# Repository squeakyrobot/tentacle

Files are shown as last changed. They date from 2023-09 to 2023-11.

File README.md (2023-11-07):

# tentacle
Modular robotic tentacle

TODO: On the project webpage add a simple calculator to help with the tentacle setup that allows the user to
easily configure their tentacle. Also add the maths in this document

## BOM

 * Internal Bearings - [F683ZZ](https://www.amazon.com/gp/product/B07Z3DRZX9)
 * Pulley Bearings - [6700-2RS](https://www.amazon.com/gp/product/B082PR3DFZ)

## Motor Options

## 28BYJ-48
I modified these motors to be bipolar, See [this article](https://ardufocus.com/howto/28byj-48-bipolar-hw-mod/)

## TODO:

- Add NEMA-11 support
- Add NEMA-14 support
- Test different configurations
    - Spine size
        - 4mm OD, 3mm ID
        - 4mm OD, 2mm ID
        - 6mm OD, 3mm ID
    - Cable materials

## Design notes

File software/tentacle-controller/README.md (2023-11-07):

# tentacle-controller

## TODO: 
 
 - Use enable pin on/off for when the movement is stopped: GPIO19, CTRL pin 3
 - Add support for controlling two motors with one timer
 - Add readme content
 - ACCESSORY: Use TMF8820 or equivalent for homing?

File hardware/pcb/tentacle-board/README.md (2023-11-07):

# Tentacle Controller PCB

TODO: Add more details about the board

## Pinout

Both motors share microstep configuration pins and the enable pin.

### Microstep Configuration

| **DRV8825 Pin** 	| **RP2040 Pin** 	|
|---	|---	|
| MODE 0 	| GPIO3 	|
| MODE 1 	| GPIO2 	|
| MODE 2 	| GPIO1 	|

### Motor A

| **DRV8825 Pin** 	| **RP2040 Pin** 	|
|---	|---	|
| DIR 	| GPIO6 	|
| STEP 	| GPIO4 	|
| ENABLE 	| GPIO5 	|
| SLEEP 	| GPIO8 	|
| RESET 	| GPIO9 	|
| HOME 	| GPIO0 	|
| FAULT 	| GPIO7 	|

### Motor B

| **DRV8825 Pin** 	| **RP2040 Pin** 	|
|---	|---	|
| DIR 	| GPIO12 	|
| STEP 	| GPIO11 	|
| ENABLE 	| GPIO5 	|
| SLEEP 	| GPIO14 	|
| RESET 	| GPIO15 	|
| HOME 	| GPIO10 	|
| FAULT 	| GPIO13 	|

### Debug Connector

| **Connector Pin** | **RP2040 Pin** |
|---	|---|
| 1 	| SWCLK |
| 2 	 | GND 	 |
| 3 	 | SWD 	 |

### UART Connector

| **Connector Pin** | **RP2040 Pin** | **Pin Functions** |
|---	|--- |--- |
| 1 	| GPIO17 | UART0 RX |
| 2 	 | GND 	 | |
| 3 	 | GPIO16 | UART0 TX |

### CTRL Connector

| **Connector Pin** | **RP2040 Pin** | **Pin Functions** |
|---	|--- |--- |
| 1 	| GND | |
| 2 	 | RUN 	 | Reset when driven low |
| 3 	 | GPIO19 | |
| 4 	 | GPIO20 | UART1 TX, I2C0 SDA |
| 5 	 | GPIO21 | UART1 RX, I2C0 SCL |

### AUX1 Connector

| **Connector Pin** | **RP2040 Pin** | **Pin Functions** |
|---	|--- |--- |
| 1 	| GND | |
| 2 	 | GPIO22 	 | |
| 3 	 | GPIO23 | |
| 4 	 | GPIO24 | |
| 5 	 | GPIO25 | |

### AUX2 Connector

| **Connector Pin** | **RP2040 Pin** | **Pin Functions** |
|---	|--- |--- |
| 1 	| GND | |
| 2 	 | GPIO26 	 | ADC0 |
| 3 	 | GPIO27 | ADC1 |
| 4 	 | GPIO28 | ADC2 |
| 5 	 | GPIO29 | ADC3 |

### Motor Connectors

All motor connectors map to the same pins of their corresponding DRV8825 modules 

| **Connector Pin** | **DRV8825 Pin** |
|---	|---	|
| 1 	| B2 	 |
| 2 	 | B1 	 |
| 3 	 | A1 	 |
| 4 	 | A2 	 |

## Revision History

### v1.0

 * Initial Release

### v1.1

 * **NOT COMPLETE**
 * Fix issue with missing silkscreen items

## TODO:

 * Investigate alternative motor connectors
    - Change to JST-PH 2mm
 * Investigate alternative power connector
 * Switch interface connectors to right angle
 * Switch to a shared SLEEP and individual ENABLE
 * Add software configurable VREF, perhaps have the pot be the max
 * Make CTRL & AUX connectors 90 degrees

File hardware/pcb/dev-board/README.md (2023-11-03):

# Development Board

TODO: Add more details about the board

## Pinout

### Microstep Configuration

Both motors share microstep configuration pins

| **DRV8825 Pin** 	| **Pico Pin** 	|
|---	|---	|
| MODE 0 	| GPIO2 	|
| MODE 1 	| GPIO3 	|
| MODE 2 	| GPIO4 	|

### Motor 1

| **DRV8825 Pin** 	| **Pico Pin** 	 |
|---	|--- |
| DIR 	| GPIO7 	|
| STEP 	| GPIO6 	|
| ENABLE 	| GND 	 |
| SLEEP 	| GPIO8 	|
| RESET 	| GND 	 |
| FAULT 	| GND 	 |

### Motor 2

| **DRV8825 Pin** 	| **Pico Pin** 	 |
|---	|--- |
| DIR 	| GPIO10 	|
| STEP 	| GPIO9 	|
| ENABLE 	| GND 	 |
| SLEEP 	| GPIO8 	|
| RESET 	| GND 	 |
| FAULT 	| GND 	 |

### Motor 3

| **DRV8825 Pin** 	| **Pico Pin** 	 |
|---	|--- |
| DIR 	| GPIO13 	|
| STEP 	| GPIO12 	|
| ENABLE 	| GND 	 |
| SLEEP 	| GPIO11 	|
| RESET 	| GND 	 |
| FAULT 	| GND 	 |

### Motor 4

| **DRV8825 Pin** 	| **Pico Pin** 	 |
|---	|--- |
| DIR 	| GPIO16 	|
| STEP 	| GPIO15 	|
| ENABLE 	| GND 	 |
| SLEEP 	| GPIO14 	|
| RESET 	| GND 	 |
| FAULT 	| GND 	 |

### Motor Connectors

All motor connectors map to the same pins of their corresponding DRV8825 modules 

| **Connector Pin** | **DRV8825 Pin** |
|---	|---	|
| 1 	| B2 	 |
| 2 	 | B1 	 |
| 3 	 | A1 	 |
| 4 	 | A2 	 |

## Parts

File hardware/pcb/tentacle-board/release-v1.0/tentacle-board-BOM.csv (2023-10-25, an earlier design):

Id | Designator | Footprint | Quantity | Designation | LCSC Part Number
1 | C37,C30,C10 | C_0805_2012Metric | 3 | 10uF | C15850
2 | C12,C11 | C_0402_1005Metric | 2 | 1uF | C107372
3 | C25,C15,C8,C27,C28,C29,C31,C32,C14,C34 | C_0402_1005Metric | 10 | 100nF | C60474
4 | U3 | SOT-223-3_TabPin2 | 1 | NCP1117-3.3_SOT223 | C2902118
5 | C26,C33 | C_0402_1005Metric | 2 | 30pF | C107004
6 | U4 | RP2040-QFN-56 | 1 | RP2040 | C2040
7 | R11 | C_0402_1005Metric | 1 | 1k | C11702
8 | Y1 | ABM810000MHZ12D2W | 1 | ABM8-12.000MHZ-20-B1U-T | C133334
9 | VR1 | TC33X2503E | 1 | TC33X-2-103E | C719176
10 | J7,J2,J5 | JST_SH_BM05B-SRSS-TB_1x05-1MP_P1.00mm_Vertical | 1 | JST_SH_BM05B | C160391
11 | L7,L6,L2,L8,L5,L1,L3,L4 | L_0805_2012Metric | 8 | L_Ferrite | C369519
12 | R6,R3,R4,R10 | R_0402_1005Metric_Pad0.72x0.64mm_HandSolder | 4 | 0.1ohms | C3013344
13 | R5,R1 | R_0402_1005Metric_Pad0.72x0.64mm_HandSolder | 2 | 1M | C138033
14 | C20,C2,C22,C23,C5,C6,C36,C7 | C_0805_2012Metric | 8 | 1nF | C51210
15 | C35,C17 | C_0603_1608Metric | 2 | 0.47uF | C577418
17 | J4,J1 | JST_XH_B4B-XH-A_1x04_P2.50mm_Vertical | 2 | Motor | C37815
18 | J6,J3 | JST_SH_BM03B-SRSS-TB_1x03-1MP_P1.00mm_Vertical | 1 | BM03B-SRSS | C160389
19 | C4,C19 | C_0603_1608Metric_Pad1.08x0.95mm_HandSolder | 2 | 10nF | C100042
20 | C3,C16,C1,C18,C21,C13 | C_0603_1608Metric_Pad1.08x0.95mm_HandSolder | 6 | 0.1uf | C3011705
21 | R12,R7,R2 | R_0402 | 2 | 10k | C60490
23 | C9,C24 | CAPAE660X800N | 2 | 100uF | C250945
24 | U1,U2 | IC_TPS61196PWPRQ1 | 2 | DRV8825PWP | C81582
25 | IC1 | SON127P600X500X80-9N-D | 1 | W25Q32JVZPIQ | C571260
26 | R9,R8,R13 | R_0402_1005Metric_Pad0.72x0.64mm_HandSolder | 3 | 1.5k | C114759
29 | J8 | JST_XH_B2B-XH-A_1x02_P2.50mm_Vertical | 1 | Power | C442299

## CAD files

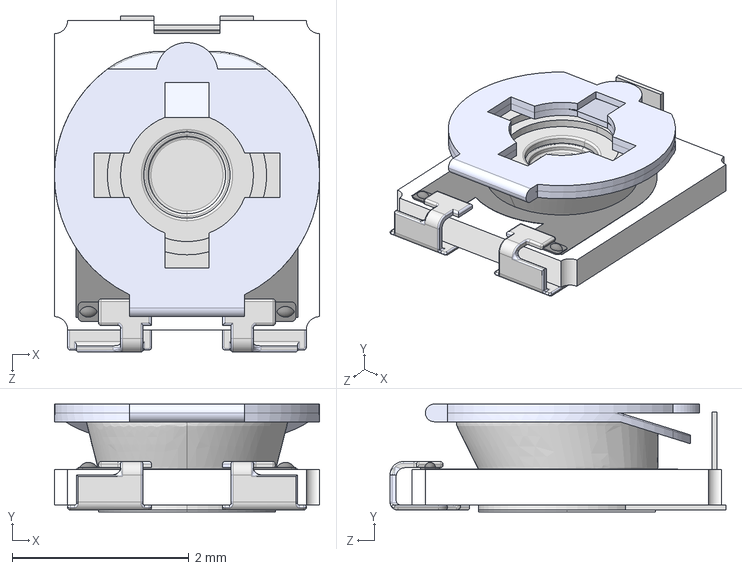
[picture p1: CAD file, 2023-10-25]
hardware/pcb/tentacle-board/3dshapes/TC33X-2-103E.stp
3.00 x 1.22 x 3.80 mm

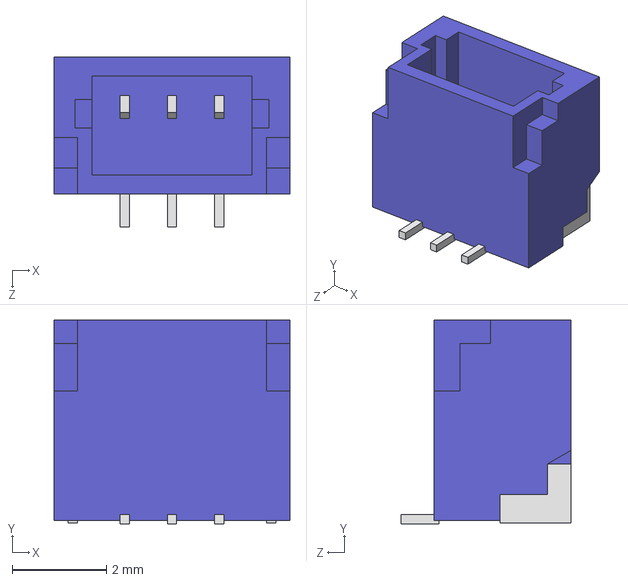
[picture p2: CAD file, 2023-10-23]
hardware/pcb/tentacle-board/3dshapes/BM03B-SRSS-TB.STEP
5.00 x 4.32 x 3.60 mm

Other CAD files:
hardware/cad/printing/assembly-tools/solder-jig.stl
hardware/cad/printing/base-lid_28BYJ-48_insert-venty.stl
hardware/cad/printing/test-stand/tent-stand-leg.stl
hardware/cad/printing/X1C/tentacle-all.3mf
hardware/cad/termination-vertebrae.step
hardware/pcb/dev-board/3dshapes/CON-SOCJ-2155.step
hardware/pcb/tentacle-board/tentacle-board.step
hardware/printing/base-lid_28BYJ-48-6-bearings.stl
hardware/cad/printing/assembly-tools/pulley-cap.stl
hardware/cad/printing/Pulley-28BYJ-48_A.stl
hardware/cad/printing/test-stand/tent-stand-top-table.stl
hardware/cad/printing/X1C/base.3mf
hardware/cad/printing/assembly-tools/termination-hold-down-jig.stl
hardware/cad/printing/base-lid-board-mount.stl
hardware/cad/printing/test-stand/tent-stand-base.stl
hardware/cad/printing/X1C/Pulley-28BYJ-48_PC.3mf
hardware/cad/printing/6mm-quick-connect-clip.stl
hardware/cad/printing/Pulley-28BYJ-48_B.stl
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

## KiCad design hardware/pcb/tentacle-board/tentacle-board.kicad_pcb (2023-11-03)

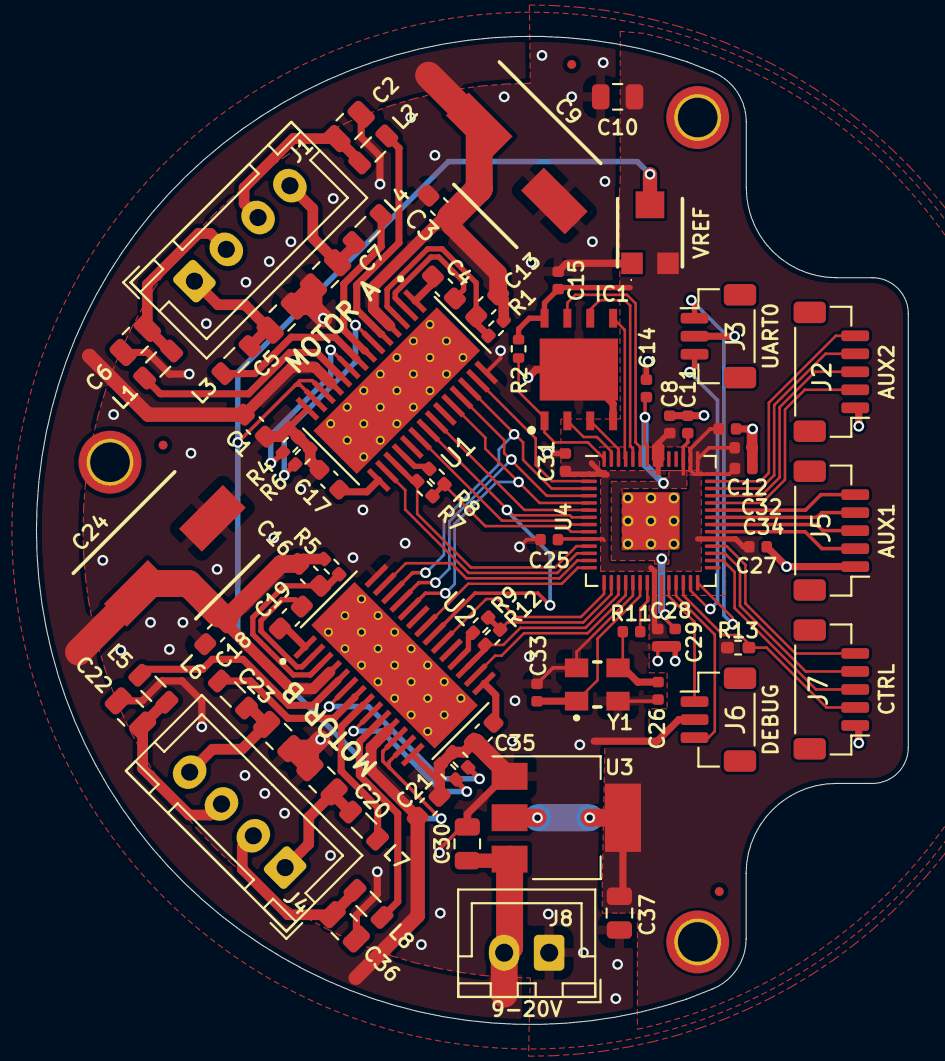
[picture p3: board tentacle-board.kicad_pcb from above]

Board: 2 copper layers, 48.4 x 54.9 mm, 79 parts (0 on the bottom side), 76 nets.

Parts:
C1, C3, C13, C16, C18, C21: 0.1uf; C_0603_1608Metric_Pad1.08x0.95mm_HandSolder
C2, C5, C6, C7, C20, C22, C23, C36: 1nF; C_0805_2012Metric
C4, C19: 10nF; C_0603_1608Metric_Pad1.08x0.95mm_HandSolder
C8, C14, C15, C25, C27, C28, C29, C31, C32, C34: 100nF; C_0402_1005Metric
C9, C24: 100uF; CAPAE660X800N
C10, C30, C37: 10uF; C_0805_2012Metric
C11, C12: 1uF; C_0402_1005Metric
C17, C35: 0.47uF; C_0603_1608Metric
C26, C33: 30pF; C_0402_1005Metric
FID1, FID2, FID3: Fiducial; Fiducial_0.5mm_Mask1mm
H1, H2, H3: MountingHole; MountingHole_2.2mm_M2_ISO7380_Pad_TopBottom
IC1: W25Q32JVZPIQ; SON127P600X500X80-9N-D
J1, J4: Motor; JST_XH_B4B-XH-A_1x04_P2.50mm_Vertical
J2: AUX2; JST_SH_BM05B-SRSS-TB_1x05-1MP_P1.00mm_Vertical
J3: UART0; JST_SH_BM03B-SRSS-TB_1x03-1MP_P1.00mm_Vertical
J5: AUX1; JST_SH_BM05B-SRSS-TB_1x05-1MP_P1.00mm_Vertical
J6: DEBUG; JST_SH_BM03B-SRSS-TB_1x03-1MP_P1.00mm_Vertical
J7: CTRL; JST_SH_BM05B-SRSS-TB_1x05-1MP_P1.00mm_Vertical
J8: Conn_01x02; JST_XH_B2B-XH-A_1x02_P2.50mm_Vertical
L1, L2, L3, L4, L5, L6, L7, L8: L_Ferrite; L_0805_2012Metric
R1, R5: 1M; R_0402_1005Metric_Pad0.72x0.64mm_HandSolder
R2: 10k; R_0402_1005Metric
R3, R4, R6, R10: 0.1; R_0402_1005Metric_Pad0.72x0.64mm_HandSolder
R7, R12: 10k; R_0402_1005Metric_Pad0.72x0.64mm_HandSolder
R8, R9, R13: 1.5k; R_0402_1005Metric_Pad0.72x0.64mm_HandSolder
R11: 1k; C_0402_1005Metric
U1, U2: DRV8825PWP; IC_TPS61196PWPRQ1
U3: NCP1117-3.3_SOT223; SOT-223-3_TabPin2
U4: RP2040; RP2040-QFN-56
VR1: TC33X-2-103E; TC33X2503E
Y1: ABM8-12.000MHZ-20-B1U-T; ABM810000MHZ12D2W

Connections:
+1V1: C11.1, C14.1, C29.1, U4.23 (DVDD), U4.45 (VREG_VOUT), U4.50 (DVDD)
+3V3: C8.1, C10.1, C12.1, C15.1, C25.1, C27.1, C28.1, C31.1, C32.1, C34.1, C37.1, IC1.8 (VCC), R2.1, R13.2, U3.2 (VO), U4.1 (IOVDD), U4.10 (IOVDD), U4.22 (IOVDD), U4.33 (IOVDD), U4.42 (IOVDD), U4.43 (ADC_AVDD), U4.44 (VREG_IN), U4.48 (USB_VDD), U4.49 (IOVDD), VR1.3 (CW)
/GPIO0: U1.27 (NHOME), U4.2 (GPIO0)
/GPIO1: U1.26 (MODE2), U2.26 (MODE2), U4.3 (GPIO1)
/GPIO2: U1.25 (MODE1), U2.25 (MODE1), U4.4 (GPIO2)
/GPIO3: U1.24 (MODE0), U2.24 (MODE0), U4.5 (GPIO3)
/GPIO4: U1.22 (STEP), U4.6 (GPIO4)
/GPIO5: U1.21 (NENBL), U2.21 (NENBL), U4.7 (GPIO5)
/GPIO6: U1.20 (DIR), U4.8 (GPIO6)
/GPIO7: R7.1, R8.2, U4.9 (GPIO7)
/GPIO8: R7.2, U1.17 (NSLEEP), U4.11 (GPIO8)
/GPIO9: U1.16 (~NRESET), U4.12 (GPIO9)
/GPIO10: U2.27 (NHOME), U4.13 (GPIO10)
/GPIO11: U2.22 (STEP), U4.14 (GPIO11)
/GPIO12: U2.20 (DIR), U4.15 (GPIO12)
/GPIO13: R9.2, R12.1, U4.16 (GPIO13)
/GPIO14: R12.2, U2.17 (NSLEEP), U4.17 (GPIO14)
/GPIO15: U2.16 (~NRESET), U4.18 (GPIO15)
/GPIO16: J3.3, U4.27 (GPIO16)
/GPIO17: J3.1, U4.28 (GPIO17)
/GPIO19: J7.3, U4.30 (GPIO19)
/GPIO20: J7.4, U4.31 (GPIO20)
/GPIO21: J7.5, U4.32 (GPIO21)
/GPIO22: J5.2, U4.34 (GPIO22)
/GPIO23: J5.3, U4.35 (GPIO23)
/GPIO24: J5.4, U4.36 (GPIO24)
/GPIO25: J5.5, U4.37 (GPIO25)
/GPIO26_ADC0: J2.2, U4.38 (GPIO26_ADC0)
/GPIO27_ADC1: J2.3, U4.39 (GPIO27_ADC1)
/GPIO28_ADC2: J2.4, U4.40 (GPIO28_ADC2)
/GPIO29_ADC3: J2.5, U4.41 (GPIO29_ADC3)
/Motor Driver A/A1: C2.1, J1.3, L2.2
/Motor Driver A/A2: C7.1, J1.4, L4.2
/Motor Driver A/B1: C6.1, J1.2, L1.2
/Motor Driver A/B2: C5.1, J1.1, L3.2
/Motor Driver A/VREF: U1.12 (AVREF), U1.13 (BVREF), U2.12 (AVREF), U2.13 (BVREF), VR1.2 (WIPER)
/Motor Driver B/A1: C22.1, J4.3, L5.2
/Motor Driver B/A2: C23.1, J4.4, L6.2
/Motor Driver B/B1: C36.1, J4.2, L8.2
/Motor Driver B/B2: C20.1, J4.1, L7.2
/QSPI_SCLK: IC1.6 (CLK), U4.52 (QSPI_SCLK)
/QSPI_SD0: IC1.5 (DI_(IO0)), U4.53 (QSPI_SD0)
/QSPI_SD1: IC1.2 (DO_(IO1)), U4.55 (QSPI_SD1)
/QSPI_SD2: IC1.3 (~WP_(IO2)), U4.54 (QSPI_SD2)
/QSPI_SD3: IC1.7 (~RESET_(IO3)), U4.51 (QSPI_SD3)
/QSPI_SS: IC1.1 (~CS), R2.2, U4.56 (QSPI_SS)
/RUN: J7.2, R13.1, U4.26 (RUN)
/SWCLK: J6.1, U4.24 (SWCLK)
/SWD: J6.3, U4.25 (SWD)
/XIN: C33.1, U4.20 (XIN), Y1.1 (X1)
/XOUT: R11.1, U4.21 (XOUT)
GND: C1.2, C2.2, C3.2, C5.2, C6.2, C7.2, C8.2, C9.2, C10.2, C11.2, C12.2, C14.2, C15.2, C17.2, C18.2, C20.2, C21.2, C22.2, C23.2, C24.2, C25.2, C26.2, C27.2, C28.2, C29.2, C30.2, C31.2, C32.2, C33.2, C34.2, C35.2, C36.2, C37.2, IC1.4 (GND), IC1.9 (EP), J2.1, J3.2, J5.1, J6.2, J7.1, J8.1, R3.2, R4.2, R6.2, R10.2, U1.14 (GND), U1.28 (GND__1), U2.14 (GND), U2.28 (GND__1), U3.1 (GND), U4.19 (TESTEN), U4.57 (GND), VR1.1 (CCW), Y1.2 (GND_1), Y1.4 (GND_2)
unnamed: L2.1, U1.5 (AOUT1)
unnamed: L4.1, U1.7 (AOUT2)
unnamed: L1.1, U1.10 (BOUT1)
unnamed: L3.1, U1.8 (BOUT2)
unnamed: C4.1, U1.1 (CP1)
unnamed: C4.2, U1.2 (CP2)
unnamed: R6.1, U1.6 (ISENA)
unnamed: R4.1, U1.9 (ISENB)
unnamed: R8.1, U1.18 (NFAULT)
unnamed: C17.1, U1.15 (V3P3OUT)
unnamed: C13.1, R1.2, U1.3 (VCP)
unnamed: L5.1, U2.5 (AOUT1)
unnamed: L6.1, U2.7 (AOUT2)
unnamed: L8.1, U2.10 (BOUT1)
unnamed: L7.1, U2.8 (BOUT2)
unnamed: C19.1, U2.1 (CP1)
unnamed: C19.2, U2.2 (CP2)
unnamed: R10.1, U2.6 (ISENA)
unnamed: R3.1, U2.9 (ISENB)
unnamed: R9.1, U2.18 (NFAULT)
unnamed: C35.1, U2.15 (V3P3OUT)
unnamed: C16.1, R5.2, U2.3 (VCP)
unnamed: C26.1, R11.2, Y1.3 (X2)
VDC: C1.1, C3.1, C9.1, C13.2, C16.2, C18.1, C21.1, C24.1, C30.1, J8.2, R1.1, R5.1, U1.4 (VMA), U1.11 (VMB), U2.4 (VMA), U2.11 (VMB), U3.3 (VI)

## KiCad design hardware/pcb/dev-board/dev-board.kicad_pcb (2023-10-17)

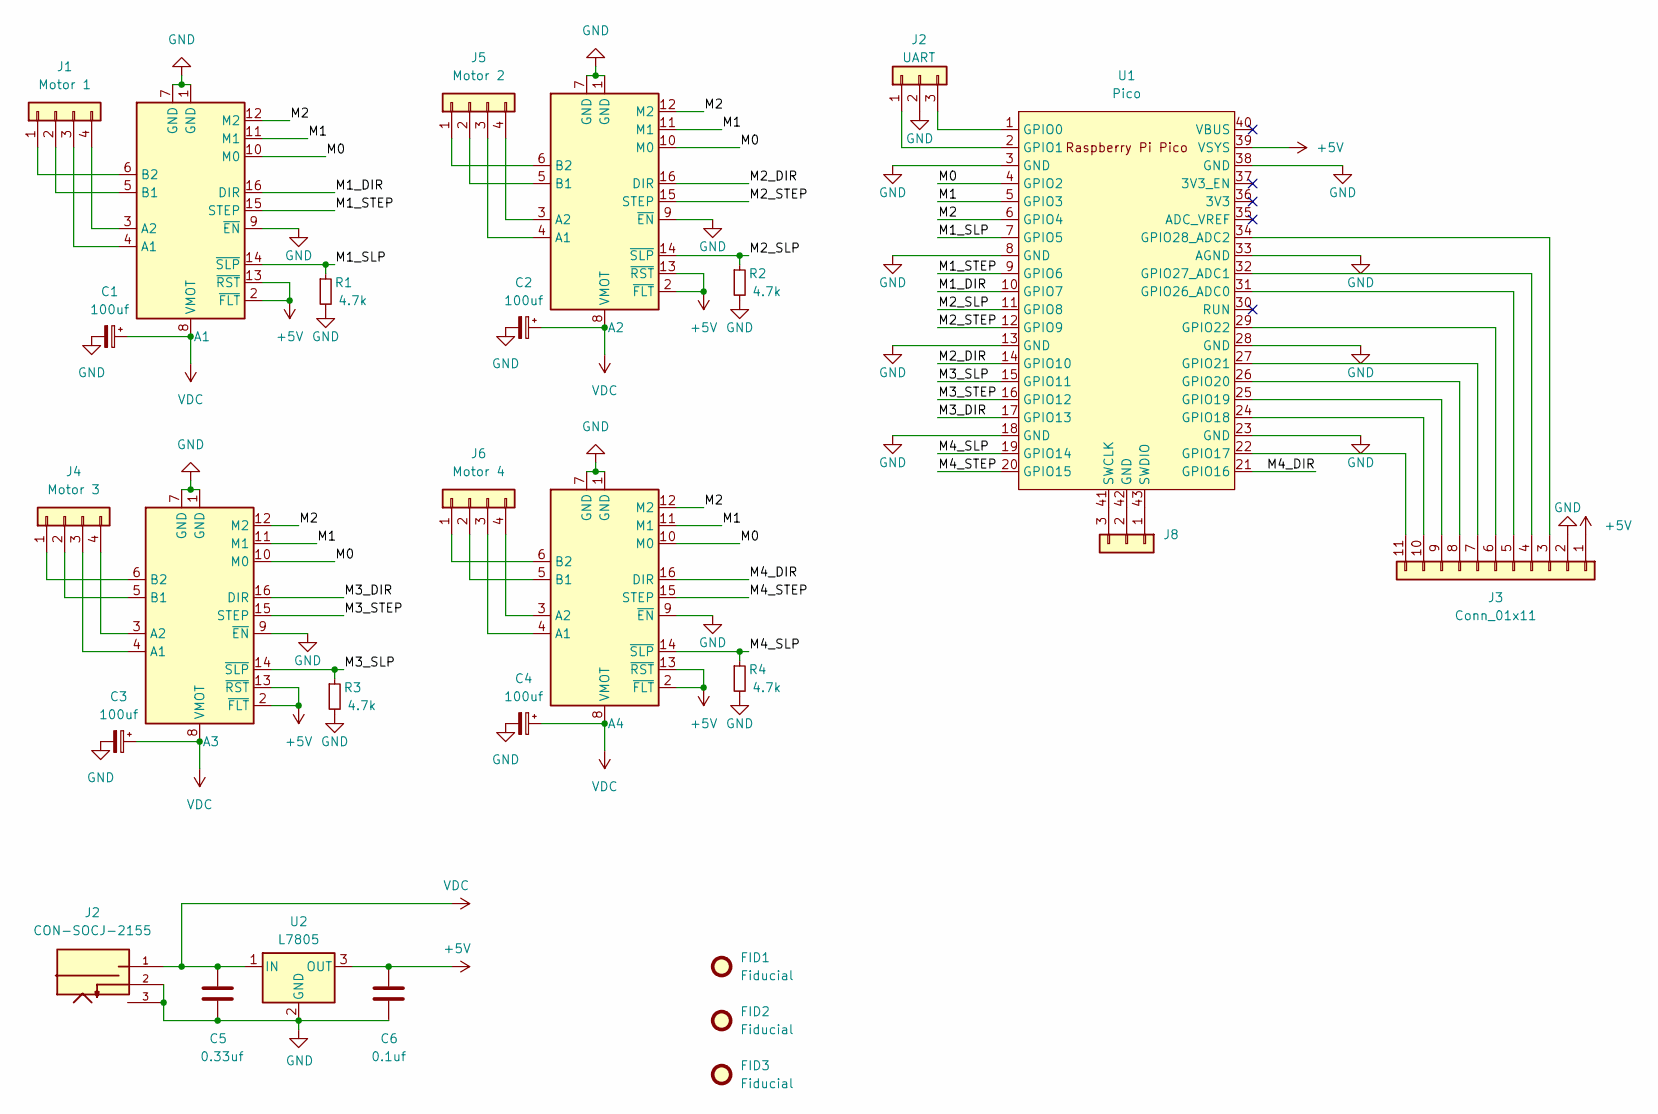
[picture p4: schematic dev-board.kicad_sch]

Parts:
A1, A2, A3, A4: Pololu_Breakout_DRV8825; Pololu_Breakout-16_15.2x20.3mm
C1, C2, C3, C4: 100uf; CP_Radial_D6.3mm_P2.50mm
C5: 0.33uf; C_0805_2012Metric_Pad1.18x1.45mm_HandSolder; Mfg # C0805C224K1RACTU; Mouser # 80-C0805C224K1R
C6: 0.1uf; C_0805_2012Metric_Pad1.18x1.45mm_HandSolder; Mfr # KGM21NR71H104KT; Mouser # 581-KGM21NR71H104KT
FID1, FID2, FID3: Fiducial; Fiducial_1mm_Mask2mm
J1: Motor 1; JST_XH_B4B-XH-A_1x04_P2.50mm_Vertical
J2: CON-SOCJ-2155; GRAVITECH_CON-SOCJ-2155; PARTREV NA
J3: Conn_01x11; PinHeader_1x11_P2.54mm_Vertical
J4: Motor 3; JST_XH_B4B-XH-A_1x04_P2.50mm_Vertical
J5: Motor 2; JST_XH_B4B-XH-A_1x04_P2.50mm_Vertical
J6: Motor 4; JST_XH_B4B-XH-A_1x04_P2.50mm_Vertical
J8: Conn_01x03; JST_XH_B3B-XH-A_1x03_P2.50mm_Vertical
R1, R2, R3, R4: 4.7k; R_0805_2012Metric_Pad1.20x1.40mm_HandSolder; Mfg # ERJ-HP6D4701V; Mouser # 667-ERJ-HP6D4701V
U1: Pico; RPi_Pico_SMD_TH
U2: L7805; TO-220-3_Vertical; Mfg # LM7805CT/NOPB

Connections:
+5V: A1.2 (~FLT), A1.13 (~RST), A2.2 (~FLT), A2.13 (~RST), A3.2 (~FLT), A3.13 (~RST), A4.2 (~FLT), A4.13 (~RST), C6.1, J3.1, U1.39 (VSYS), U2.3 (OUT)
/M0: A1.10 (M0), A2.10 (M0), A3.10 (M0), A4.10 (M0), U1.4 (GPIO2)
/M1: A1.11 (M1), A2.11 (M1), A3.11 (M1), A4.11 (M1), U1.5 (GPIO3)
/M1_DIR: A1.16 (DIR), U1.10 (GPIO7)
/M1_SLP: A1.14 (~SLP), R1.1, U1.7 (GPIO5)
/M1_STEP: A1.15 (STEP), U1.9 (GPIO6)
/M2: A1.12 (M2), A2.12 (M2), A3.12 (M2), A4.12 (M2), U1.6 (GPIO4)
/M2_DIR: A2.16 (DIR), U1.14 (GPIO10)
/M2_SLP: A2.14 (~SLP), R2.1, U1.11 (GPIO8)
/M2_STEP: A2.15 (STEP), U1.12 (GPIO9)
/M3_DIR: A3.16 (DIR), U1.17 (GPIO13)
/M3_SLP: A3.14 (~SLP), R3.1, U1.15 (GPIO11)
/M3_STEP: A3.15 (STEP), U1.16 (GPIO12)
/M4_DIR: A4.16 (DIR), U1.21 (GPIO16)
/M4_SLP: A4.14 (~SLP), R4.1, U1.19 (GPIO14)
/M4_STEP: A4.15 (STEP), U1.20 (GPIO15)
unnamed: A1.4 (A1), J1.3
unnamed: A1.3 (A2), J1.4
unnamed: A1.5 (B1), J1.2
unnamed: A1.6 (B2), J1.1
unnamed: A2.4 (A1), J5.3
unnamed: A2.3 (A2), J5.4
unnamed: A2.5 (B1), J5.2
unnamed: A2.6 (B2), J5.1
unnamed: A3.4 (A1), J4.3
unnamed: A3.3 (A2), J4.4
unnamed: A3.5 (B1), J4.2
unnamed: A3.6 (B2), J4.1
unnamed: A4.4 (A1), J6.3
unnamed: A4.3 (A2), J6.4
unnamed: A4.5 (B1), J6.2
unnamed: A4.6 (B2), J6.1
unnamed: J3.3, U1.34 (GPIO28_ADC2)
unnamed: J3.4, U1.32 (GPIO27_ADC1)
unnamed: J3.5, U1.31 (GPIO26_ADC0)
unnamed: J3.6, U1.29 (GPIO22)
unnamed: J3.7, U1.27 (GPIO21)
unnamed: J3.8, U1.26 (GPIO20)
unnamed: J3.9, U1.25 (GPIO19)
unnamed: J3.10, U1.24 (GPIO18)
unnamed: J3.11, U1.22 (GPIO17)
unnamed: J8.1, U1.43 (SWDIO)
unnamed: J8.2, U1.42 (GND)
unnamed: J8.3, U1.41 (SWCLK)

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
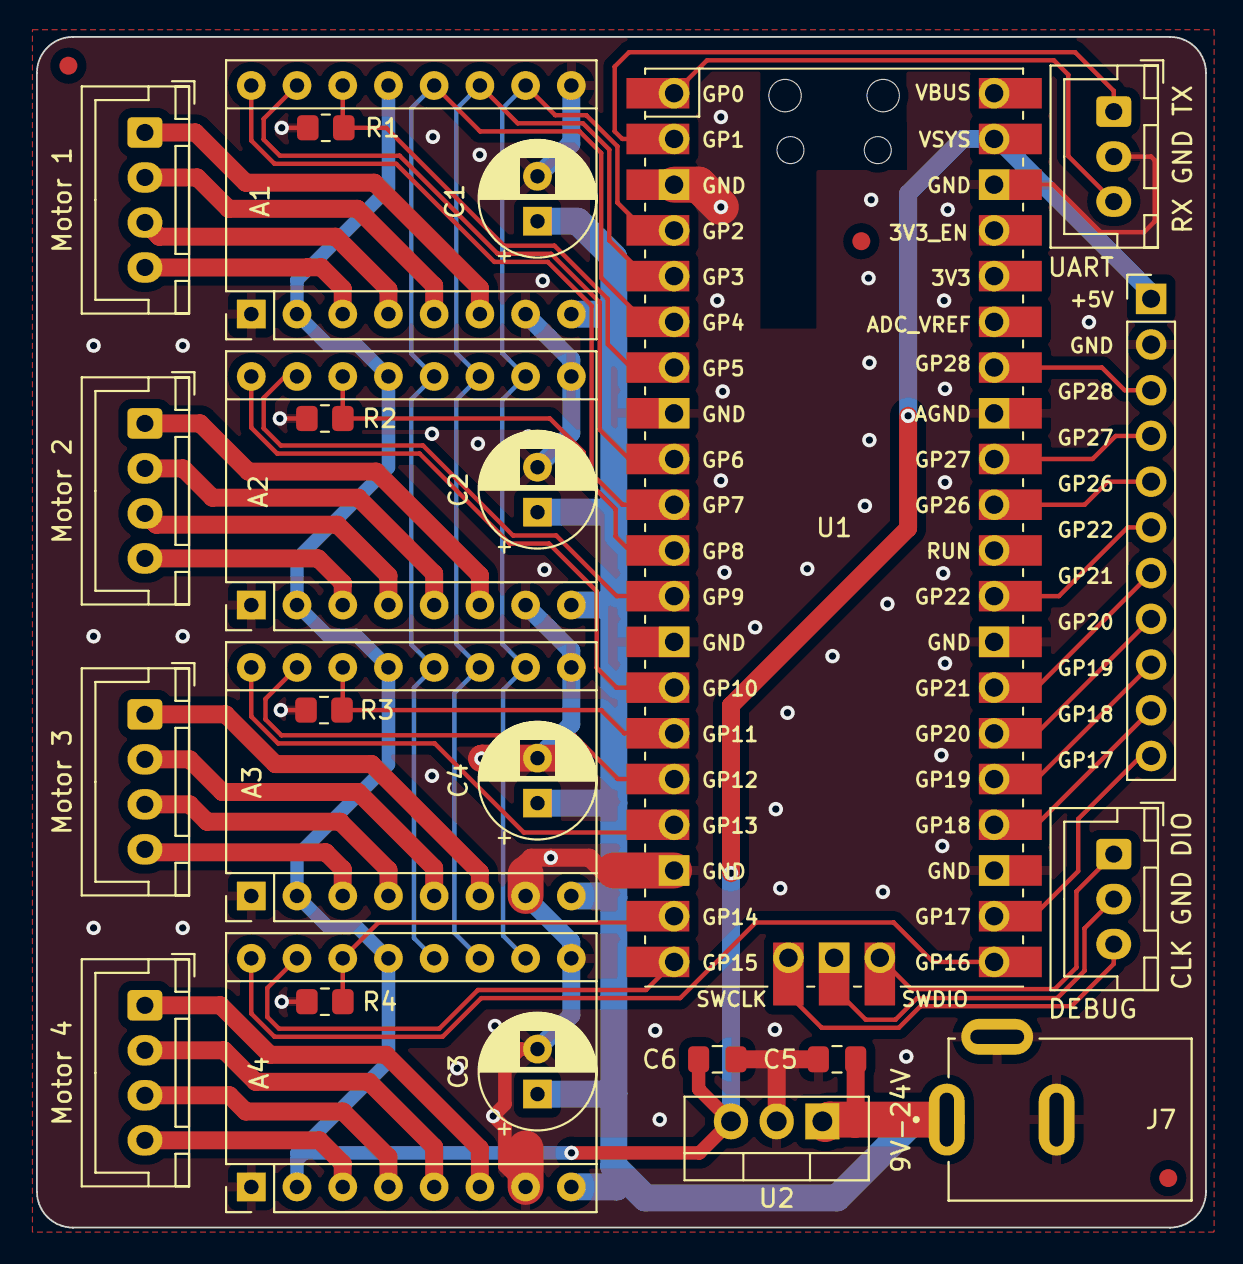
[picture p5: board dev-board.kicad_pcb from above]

Board: 2 copper layers, 64.9 x 66.2 mm, 27 parts (0 on the bottom side), 48 nets.

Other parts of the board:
J7: CON-SOCJ-2155; GRAVITECH_CON-SOCJ-2155

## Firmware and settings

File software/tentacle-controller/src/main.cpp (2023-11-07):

#include <stdio.h>
#include <time.h>

#include "driver-configuration.h"
#include "pico/stdlib.h"
#include "tentacle-controller.h"
#include "timer-stepper-driver.h"
#include "util.h"

// TODO:
// 1. Create class - DONE
// 2. Be able to move n degrees - DONE
// 3. Be able to set limits - DONE
// 4. Be able to stop moving - DONE
// 5. Maybe track degrees moved, or location from start
//   5.1 Clockwise = positive, CounterClockwise = negative???
//   5.2 Sensorless homing to set start point???

// 0-255
#define SPEED 128

int main() {
    stdio_init_all();
    puts("Starting");

    // Setup micro stepping -
    // TODO: wrap this into an easy to use function
    gpio_init(MODE0_PIN);
    gpio_set_dir(MODE0_PIN, GPIO_OUT);
    gpio_put(MODE0_PIN, 1);

    gpio_init(MODE1_PIN);
    gpio_set_dir(MODE1_PIN, GPIO_OUT);
    gpio_put(MODE1_PIN, 0);

    gpio_init(MODE2_PIN);
    gpio_set_dir(MODE2_PIN, GPIO_OUT);
    gpio_put(MODE2_PIN, 0);

    // // Enable - NOT REQUIRED
    // gpio_init(MOTOR_ENABLE_PIN);
    // gpio_set_dir(MOTOR_ENABLE_PIN, GPIO_OUT);
    // gpio_put(MOTOR_ENABLE_PIN, 0);

    // Sleep - REQUIRED
    gpio_init(MOTOR_A_SLEEP_PIN);
    gpio_set_dir(MOTOR_A_SLEEP_PIN, GPIO_OUT);
    gpio_put(MOTOR_A_SLEEP_PIN, 1);

    gpio_init(MOTOR_B_SLEEP_PIN);
    gpio_set_dir(MOTOR_B_SLEEP_PIN, GPIO_OUT);
    gpio_put(MOTOR_B_SLEEP_PIN, 1);

    // Reset - REQUIRED
    gpio_init(MOTOR_A_RESET_PIN);
    gpio_set_dir(MOTOR_A_RESET_PIN, GPIO_OUT);
    gpio_put(MOTOR_A_RESET_PIN, 1);

    gpio_init(MOTOR_B_RESET_PIN);
    gpio_set_dir(MOTOR_B_RESET_PIN, GPIO_OUT);
    gpio_put(MOTOR_B_RESET_PIN, 1);

    TentacleConfig config;
    // config.driver1Config = createMotorConfig(DRV8825_28BYJ48_64, 6, 7);
    // config.driver2Config = createMotorConfig(DRV8825_28BYJ48_64, 9, 10);

    config.driver1Config = createMotorConfig(DRV8825_NEMA11, MOTOR_A_STEP_PIN, MOTOR_A_DIR_PIN, MOTOR_A_SLEEP_PIN);
    config.driver2Config = createMotorConfig(DRV8825_NEMA11, MOTOR_B_STEP_PIN, MOTOR_B_DIR_PIN, MOTOR_B_SLEEP_PIN);

    TentacleController *tc = TentacleController::create(config);

    tc->setSpeed(220);

    tc->moveTo(20, 0);
    while (tc->getStatus() == Moving) {
        sleep_ms(100);
    }

    tc->moveTo(0, 0);
    while (tc->getStatus() == Moving) {
        sleep_ms(100);
    }

    // tc->moveTo(0, 0);
    // while (tc->getStatus() == Moving) {
    //     sleep_ms(100);
    // }

    // tc->moveTo(25, 45);
    // while (tc->getStatus() == Moving) {
    //     sleep_ms(100);
    // }

    // tc->moveTo(25, 0);
    // while (tc->getStatus() == Moving) {
    //     sleep_ms(100);
    // }

    // tc->moveTo(0, 0);
    // while (tc->getStatus() == Moving) {
    //     sleep_ms(100);
    // }

    sleep_ms(1000);

    // tc->move(50, 45); // TODO: Check & fix move

    for (;;) {
        // puts("Entering Loop");

        tc->moveTo(25, 10);
        while (tc->getStatus() == Moving) {
            sleep_ms(500);
        }

        tc->moveTo(25, 90);
        while (tc->getStatus() == Moving) {
            sleep_ms(500);
        }

        tc->moveTo(25, 180);
        while (tc->getStatus() == Moving) {
            sleep_ms(500);
        }

        tc->moveTo(25, 270);
        while (tc->getStatus() == Moving) {
            sleep_ms(500);
        }

        tc->moveTo(25, 180);
        while (tc->getStatus() == Moving) {
            sleep_ms(500);
        }

        tc->moveTo(0, 0);
        while (tc->getStatus() == Moving) {
            sleep_ms(500);
        }

        sleep_ms(10000);
    }
}

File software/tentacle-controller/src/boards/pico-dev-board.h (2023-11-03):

/*
 * Copyright (c) 2020 Raspberry Pi (Trading) Ltd.
 *
 * SPDX-License-Identifier: BSD-3-Clause
 */

// -----------------------------------------------------
// NOTE: THIS HEADER IS ALSO INCLUDED BY ASSEMBLER SO
//       SHOULD ONLY CONSIST OF PREPROCESSOR DIRECTIVES
// -----------------------------------------------------

#ifndef _BOARDS_PICO_DEV_BOARD_H
#define _BOARDS_PICO_DEV_BOARD_H

// For board detection
#define PICO_DEV_BOARD

// TENTACLE CONTROLLER PIN CONFIGURATION
// --------------------------------------

#define MODE0_PIN 2
#define MODE1_PIN 3
#define MODE2_PIN 4

// Not present on dev board
// #define MOTOR_ENABLE_PIN 5

#define MOTOR_A_DIR_PIN 7
#define MOTOR_A_STEP_PIN 6
#define MOTOR_A_SLEEP_PIN 8

// Not present on dev board
// #define MOTOR_A_RESET_PIN 9
// #define MOTOR_A_HOME_PIN 0
// #define MOTOR_A_FAULT_PIN 7

#define MOTOR_1_DIR_PIN MOTOR_A_DIR_PIN
#define MOTOR_1_STEP_PIN MOTOR_A_STEP_PIN
#define MOTOR_1_SLEEP_PIN MOTOR_A_SLEEP_PIN

#define MOTOR_B_DIR_PIN 10
#define MOTOR_B_STEP_PIN 9
#define MOTOR_B_SLEEP_PIN 8

// Not present on dev board
// #define MOTOR_B_RESET_PIN 15
// #define MOTOR_B_HOME_PIN 10
// #define MOTOR_B_FAULT_PIN 13

#define MOTOR_2_DIR_PIN MOTOR_B_DIR_PIN
#define MOTOR_2_STEP_PIN MOTOR_B_STEP_PIN
#define MOTOR_2_SLEEP_PIN MOTOR_B_SLEEP_PIN

#define MOTOR_3_DIR_PIN 13
#define MOTOR_3_STEP_PIN 12
#define MOTOR_3_SLEEP_PIN 11

#define MOTOR_4_DIR_PIN 16
#define MOTOR_4_STEP_PIN 15
#define MOTOR_4_SLEEP_PIN 14

// --- UART ---
#ifndef PICO_DEFAULT_UART
#define PICO_DEFAULT_UART 0
#endif
#ifndef PICO_DEFAULT_UART_TX_PIN
#define PICO_DEFAULT_UART_TX_PIN 0
#endif
#ifndef PICO_DEFAULT_UART_RX_PIN
#define PICO_DEFAULT_UART_RX_PIN 1
#endif

// --- LED ---
#ifndef PICO_DEFAULT_LED_PIN
#define PICO_DEFAULT_LED_PIN 25
#endif
// no PICO_DEFAULT_WS2812_PIN

// --- I2C ---
#ifndef PICO_DEFAULT_I2C
#define PICO_DEFAULT_I2C 0
#endif
#ifndef PICO_DEFAULT_I2C_SDA_PIN
#define PICO_DEFAULT_I2C_SDA_PIN 4
#endif
#ifndef PICO_DEFAULT_I2C_SCL_PIN
#define PICO_DEFAULT_I2C_SCL_PIN 5
#endif

// --- SPI ---
#ifndef PICO_DEFAULT_SPI
#define PICO_DEFAULT_SPI 0
#endif
#ifndef PICO_DEFAULT_SPI_SCK_PIN
#define PICO_DEFAULT_SPI_SCK_PIN 18
#endif
#ifndef PICO_DEFAULT_SPI_TX_PIN
#define PICO_DEFAULT_SPI_TX_PIN 19
#endif
#ifndef PICO_DEFAULT_SPI_RX_PIN
#define PICO_DEFAULT_SPI_RX_PIN 16
#endif
#ifndef PICO_DEFAULT_SPI_CSN_PIN
#define PICO_DEFAULT_SPI_CSN_PIN 17
#endif

// --- FLASH ---

#define PICO_BOOT_STAGE2_CHOOSE_W25Q080 1

#ifndef PICO_FLASH_SPI_CLKDIV
#define PICO_FLASH_SPI_CLKDIV 2
#endif

#ifndef PICO_FLASH_SIZE_BYTES
#define PICO_FLASH_SIZE_BYTES (2 * 1024 * 1024)
#endif

// Drive high to force power supply into PWM mode (lower ripple on 3V3 at light loads)
#define PICO_SMPS_MODE_PIN 23

#ifndef PICO_RP2040_B0_SUPPORTED
#define PICO_RP2040_B0_SUPPORTED 1
#endif

// The GPIO Pin used to read VBUS to determine if the device is battery powered.
#ifndef PICO_VBUS_PIN
#define PICO_VBUS_PIN 24
#endif

// The GPIO Pin used to monitor VSYS. Typically you would use this with ADC.
// There is an example in adc/read_vsys in pico-examples.
#ifndef PICO_VSYS_PIN
#define PICO_VSYS_PIN 29
#endif

#endif

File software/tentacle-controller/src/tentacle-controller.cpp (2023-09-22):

#include "tentacle-controller.h"

#include <cmath>

#include "timer-stepper-driver.h"

// TODO: Implement motor limits based on number of tentacle segments
//          - 4.4mm travel per segment
//          - Test tentacle: 18 segments - 79.2mm of travel - each direction
//              - Pulley: 18mm Diameter - 1.4 wraps per direction, 2.8 Total
//              - TODO: Expand pulley diameter, or make the inside diameter smaller
// TODO: Implement realtime location updates

TentacleController* TentacleController::create(TentacleConfig config) {
    // TODO: Update this to support driver type when and if we have more than one

    StepperDriver* driver1 = new TimerStepperDriver(config.driver1Config);
    StepperDriver* driver2 = new TimerStepperDriver(config.driver2Config);

    return new TentacleController(config, driver1, driver2);
}

TentacleController::~TentacleController() {
    // delete this->location;

    delete this->motor1;
    delete this->motor2;
}

bool TentacleController::move(int16_t amplitude, int16_t degrees) {
    return this->move(amplitude, degrees, this->systemSpeed);
}

bool TentacleController::move(int16_t amplitude, int16_t degrees, uint8_t speed) {
    TentacleLocation targetLocation;

    return this->move(amplitude, degrees, speed, targetLocation);
}

bool TentacleController::move(int16_t amplitude, int16_t degrees, TentacleLocation& targetLocation) {
    return this->move(amplitude, degrees, this->systemSpeed, targetLocation);
}

bool TentacleController::move(int16_t amplitude, int16_t degrees, uint8_t speed, TentacleLocation& targetLocation) {
    // Find the final target location after the move
    uint16_t angle = (degrees + 360) % 360;

    targetLocation.angle = (targetLocation.angle + angle) % 360;
    targetLocation.amplitude = clamp(targetLocation.amplitude + amplitude, 0, MAX_AMPLITUDE);

    // Find the target locatioin in motor steps
    TentacleLocationSteps locationSteps = this->calculateMotorLocation(targetLocation.amplitude, targetLocation.angle);

    // Find the difference from the current location
    this->motor1->stop();
    this->motor2->stop();
    uint32_t m1Travel = this->motor1->getStepLocation() - locationSteps.motor1Steps;
    uint32_t m2Travel = this->motor2->getStepLocation() - locationSteps.motor2Steps;

    this->motor1->rotateSteps(speed, m1Travel);
    this->motor2->rotateSteps(speed, m2Travel);

    // TODO: Figure out how to update status & location and get a callback when the move is complete

    return true;
}

bool TentacleController::moveTo(uint8_t amplitude, uint16_t angle) {
    return this->moveTo(amplitude, angle, this->systemSpeed);
}

bool TentacleController::moveTo(uint8_t amplitude, uint16_t angle, uint8_t speed) {
    angle = clampDegrees(angle);
    amplitude = clamp(amplitude, 0, MAX_AMPLITUDE);

    // Find the target locatioin in motor steps
    TentacleLocationSteps locationSteps = this->calculateMotorLocation(amplitude, angle);

    printf("M1 Target Steps: %d\n", locationSteps.motor1Steps);
    printf("\tLocation: %d\n", this->motor1->getStepLocation());

    // Find the difference from the current location
    this->motor1->stop();
    this->motor2->stop();
    uint32_t m1Travel = locationSteps.motor1Steps - this->motor1->getStepLocation();
    uint32_t m2Travel = locationSteps.motor2Steps - this->motor2->getStepLocation();

    printf("M1 Location: %d\n", this->motor1->getStepLocation());
    printf("M1 Travel Steps: %d\n", m1Travel);

    this->motor1->rotateSteps(speed, m1Travel);
    this->motor2->rotateSteps(speed, m2Travel);

    return true;
}

bool TentacleController::rotate(int16_t degrees, RotationDirection direction) {
    return this->rotate(degrees, direction, this->systemSpeed);
}

bool TentacleController::rotate(int16_t degrees, RotationDirection direction, uint8_t speed) {
    TentacleLocation targetLocation;

    return this->rotate(degrees, direction, speed, targetLocation);
}

bool TentacleController::rotate(int16_t degrees, RotationDirection direction, TentacleLocation& targetLocation) {
    return this->rotate(degrees, direction, this->systemSpeed, targetLocation);
}

bool TentacleController::rotate(int16_t degrees, RotationDirection direction, uint8_t speed, TentacleLocation& targetLocation) {
    // TODO: implement
    return false;
}

bool TentacleController::rotateTo(uint16_t angle) {
    return this->rotateTo(angle, this->systemSpeed);
}

bool TentacleController::rotateTo(uint16_t angle, uint8_t speed) {
    // return this->rotateTo(angle, this->calculateRotationPath(angle), speed);

    return false;
}

bool TentacleController::rotateTo(uint16_t angle, RotationDirection direction) {
    return this->rotateTo(angle, direction, this->systemSpeed);
}

bool TentacleController::rotateTo(uint16_t angle, RotationDirection direction, uint8_t speed) {
    // TODO: implement
    return false;
}

bool TentacleController::stop() {
    this->motor1->stop();
    this->motor2->stop();

    // TODO: figure out how the location is updated
    return true;
}

void TentacleController::resetPosition(uint8_t amplitude, uint16_t angle) {
    this->location.amplitude = amplitude;
    this->location.angle - angle;
}

void TentacleController::setSpeed(uint8_t speed) {
    this->systemSpeed = speed;
}

uint8_t TentacleController::getSpeed() {
    return this->systemSpeed;
}

MotionStatus TentacleController::getStatus() {
    return (this->motor1->getStatus() == Moving || this->motor2->getStatus() == Moving) ? Moving : Stopped;
}

// ---------------------------------------------------
// PRIVATE
//----------------------------------------------------
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

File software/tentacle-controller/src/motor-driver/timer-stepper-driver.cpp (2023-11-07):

#include "timer-stepper-driver.h"

TimerStepperDriver::TimerStepperDriver(StepperDriverConfig config) : StepperDriver(config) {
    gpio_init(config.stepPin);
    gpio_init(config.directionPin);
    gpio_set_dir(config.stepPin, GPIO_OUT);
    gpio_set_dir(config.directionPin, GPIO_OUT);
    gpio_put(config.directionPin, (this->config.invertDirection) ? !Clockwise : Clockwise);

    if (config.sleepOnStop == true) {
        gpio_init(config.sleepPin);
        gpio_set_dir(config.sleepPin, GPIO_OUT);
        gpio_put(config.sleepPin, 0);
    }

    this->stepsFromHome = 0;
};

TimerStepperDriver::~TimerStepperDriver() {
    cancel_repeating_timer(&this->timer);
};

bool TimerStepperDriver::rotateSteps(uint8_t speed, uint32_t steps, RotationDirection direction) {
    if (steps == 0) {
        return true;
    }

    if (config.sleepOnStop == true) {
        gpio_put(config.sleepPin, 1);
        // sleep_ms(10);
    }

    puts("Timer Rotate Steps");
    if (this->direction != direction) {
        this->direction = direction;
        gpio_put(this->config.directionPin, (this->config.invertDirection) ? !direction : direction);
    }

    if (this->timer.alarm_id > 0) {
        cancel_repeating_timer(&this->timer);
    }

    if (speed < 1) {
        return false;
    }

    uint32_t stepsPerSecond = this->calculateStepsPerSecond(speed);

    this->remainingSteps = steps;
    this->status = Moving;

    // It takes two timer triggers to complete one step
    uint32_t delay = stepsPerSecond * 2;

    return add_repeating_timer_us(-(1000000 / (double)delay), TimerStepperDriver::timerCallback, this, &this->timer);
};

bool TimerStepperDriver::stop() {
    this->status = Stopped;

    if (config.sleepOnStop == true) {
        gpio_put(config.sleepPin, 0);
    }

    return cancel_repeating_timer(&this->timer);
};

bool TimerStepperDriver::timerCallback(repeating_timer_t *repeatingTimer) {
    TimerStepperDriver *driver = (TimerStepperDriver *)(repeatingTimer->user_data);
    uint8_t stepPin = driver->getStepPin();

    bool stepPinValue = !gpio_get(stepPin);
    gpio_put(stepPin, stepPinValue);

    if (stepPinValue) {
        if (driver->direction == Clockwise) {
            driver->stepsFromHome++;
        } else {
            driver->stepsFromHome--;
        }

        if ((driver->remainingSteps--) <= 0) {
            printf("Move Stopped: %d\n", driver->stepsFromHome);
            driver->stop();
            return false;
        }
    }

    return true;  // keep repeating
};

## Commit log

2023-09-12 Added current stl files, and a project stub for the firmware
    [6mm-quick-connect-clip-v2.stl, 6mm-quick-connect-clip.stl, base-lid.stl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]
2023-09-12 Recreated stub pico project using https://github.com/raspberrypi/pico-project-generator
2023-09-13 Got the basic stepper driver tests done for DRV8830 and TMC2209
    [base.stl]
2023-09-13 Created the base motor driver interface and a timer based implementation
2023-09-14 Added stub for pio driver, no implementation
2023-09-15 Added the interface and stubs for the tentacle controller
    [pulley-28BYK-48_v2.stl]
2023-09-16 Added a step counter to the motor driver
2023-09-22 Added bearings to the motor base and did multiple experiments to get it functioning correctly
    [6700-2RS-pusher.stl, 6mm-quick-connect-clip-v2.stl, 6mm-quick-connect-clip.stl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]
2023-09-26 Updated CAD & some basic testing
    [6700-2RS-pusher.stl, 6mm-quick-connect-clip.stl, base-3mm-bearing-3mm-space.stl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]
2023-10-13 Updated readme with some todos
    [termination-hold-down-jig.stl, termination-vertabrea-v2.stl, termination-vertabrea.stl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]
2023-10-15 Modified the vertebrae to have a square semi-spherical joint to prevent twiasting and allow for more deterministic positioning
    [base-lid-nema-11.stl, pulley-nema-11.stl, tentacle-spacer-4.2mm.stl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]
2023-10-17 Added custom PCB to use as a development board
    [CON-SOCJ-2155.step, Pico.skp, dev-board.kicad_pcb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]
2023-10-17 Finished dev board PCB
    [dev-board-B_Cu.gbl, dev-board-B_Mask.gbs, dev-board-B_Silkscreen.gbo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]
2023-10-17 Added stub PCB for the tentacle board based on the RP2049 minimal example
    [DRV8825PWP.step, tentacle-board.kicad_pcb, tentacle-board.kicad_sch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]
2023-10-18 Added stepper drivers to the tentacle controller PCB
    [EDT107M025S9HAA.stp, motor-driver.kicad_sch, tentacle-board.kicad_pcb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]
2023-10-19 Worked on the motor power system and stepper driver BOM
    [UCD1E101MCL1GS.stp, motor-driver.kicad_sch, tentacle-board.kicad_pcb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]
2023-10-20 Added the MCU and supporting components and wired them up
    [ABM8-12.000MHZ-20-B1U-T.stp, PTS815_SJM_250_SMTR_LFS.stp, motor-driver.kicad_sch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]
2023-10-20 Updated flash to a smaller package, moved in the MCU to make some more room
    [W25Q32JVZPIQ.stp, tentacle-board.kicad_pcb, tentacle-board.kicad_sch]
2023-10-21 Updated references and formatted silkscreen layer
    [tentacle-board.kicad_pcb]
2023-10-23 Added aux plugs and updated the edge cuts
    [BM03B-SRSS-TB.STEP, tentacle-board.kicad_pcb, tentacle-board.kicad_sch]
2023-10-24 Finished component & trace layout
    [motor-driver.kicad_sch, tentacle-board.kicad_pcb, tentacle-board.kicad_sch]
2023-10-25 Finished v1 and created manufacturing outputs
    [TC33X-2-103E.stp, base.stl, motor-driver.kicad_sch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]
2023-10-25 Added some images of the assembled dev-board
2023-11-03 Updated the firmware readme with pinout of the dev board and controller board
2023-11-03 Updated the firmware project to build the custom board. Fixed some missing silkscreen items on the pcb.
    [tentacle-board-B_Cu.gbl, tentacle-board-B_Mask.gbs, tentacle-board-B_Paste.gbp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]
2023-11-03 Organized readmes and updated board definition files
2023-11-05 Modified the pulley for printing in a better orientation
    [Pulley-28BYJ-48.stl, Pulley-28BYJ-48_PC.3mf, pulley-28BYK-48_6700-2RS.stl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]
2023-11-07 Minor changes from hardware testing
    [6700-2RS-pusher.stl, Pulley-28BYJ-48.stl, Pulley-28BYJ-48_A.stl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]
